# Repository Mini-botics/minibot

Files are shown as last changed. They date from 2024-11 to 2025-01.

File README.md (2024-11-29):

# Minibot
An open-source, ROS-compatible mini robot project designed for educational purposes. Ideal for learning robotics, experimenting with ROS, or personal projects. 



## Unique Features
- **Robust and Customizable**: Offers modularity for customization with readily available components that are easy to replace or upgrade. Supports various locomotion types, including differential, 4 wheel and holonomic drive systems, allowing for customizable movement options.



- **Minimal Cable Design**: All key components (battery, charger, BMS, etc.) are integrated into a single robot using a custom PCB, minimizing wiring while ensuring both efficiency and durability.





- **Easy-to-Use**: Designed to be user-friendly for beginners while still offering enough complexity for advanced users to explore.

- **Affordable**: Engineered to be a cost-effective option for students and hobbyists alike, without sacrificing quality or performance.

## Getting Started
To get started with the robot, please follow this video documentation.

IMAGE ALT TEXT HERE (https://www.youtube.com/watch?v=GUFT_sU2eYY&t)

You can also check our [youtube channel](https://www.youtube.com/@minibotics). 

Please note that this is an open-source project, and we welcome contributions and suggestions from the community.

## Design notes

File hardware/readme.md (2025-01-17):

# Bill of Materials (BOM)

This project requires several components to build. The detailed Bill of Materials (BOM), including quantities, descriptions, and purchase links, is hosted on Google Sheets for easy access and updates.

[View the Bill of Materials on Google Sheets](https://docs.google.com/spreadsheets/d/1GKpQS9YWHXVLVaMREtha1JvgfUiriMxIkeRr4HUK7rA/edit?usp=sharing)

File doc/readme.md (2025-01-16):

# minibot PCB Design Files

Access the design files for various layers and components of the minibot project using the links below:

- **[Base Layer Design Files](https://oshwlab.com/rstmsvk/mini_copy_copy_copy_copy_copy_copy_copy_copy_copy_copy_copy)**  
  The base layer design files of the minibot.

- **[Proto Layer Design Files](https://oshwlab.com/rstmsvk/mini_copy_copy_copy_copy_copy_copy_copy_copy_copy_copy_copy_copy)**  
  The proto layer design files for the minibot.

- **[Encoder Design Files](https://oshwlab.com/rstmsvk/mini_copy_copy_copy_copy_copy_copy_copy_copy_copy_copy_copy_copy_copy_copy)**  
  The encoder design files for the minibot.

- **[Proto Board Design Files](https://oshwlab.com/rstmsvk/mini_copy_copy_copy_copy_copy_copy_copy_copy_copy_copy_copy_copy_copy)**  
  Design files for the proto board used in the minibot project.

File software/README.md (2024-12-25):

# Minibot Software
The software section of the Minibot is organized into specific folders, each serving a unique purpose, as detailed below:

**romer-minibot**: 
   - This folder contains the Pico library with wireless communication capabilities. 
   - Use this if your project requires network communication for the robot.

**romer-minibot-lite**: 
   - This folder contains a simpler version of the Pico library without wireless communication capabilities.
   - Use this version for offline or standalone functionality.

**MiniROS**:
   - This folder contains the ROS (Robot Operating System) part of the project.
   - Check this folder if you are integrating ROS into your robot project.

## Getting Started

- To integrate wireless communication, navigate to the `romer-minibot` folder and follow the setup instructions provided there.
- For a lightweight, offline version, explore the `romer-minibot-lite` folder.
- To explore the ROS implementation, check the `MiniROS` folder.

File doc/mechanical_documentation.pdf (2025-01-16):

# ME462 MECHATRONIC DESIGN

# Mini Robot Documentation

# Version 1.0

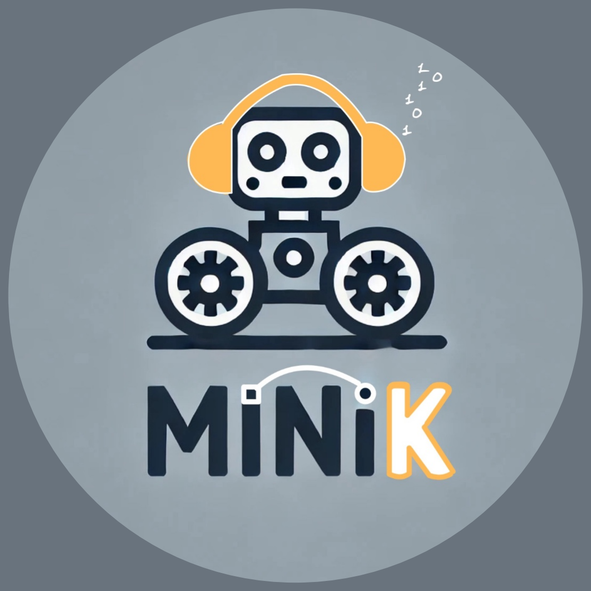
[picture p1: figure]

### MECHANICAL DOCUMENTATION

## Table of Contents

1 Introduction | 2
2 Component List | 2
3 Print Instructions | 2
3.1 Battery Holders | | 2
3.2 Wheels | | 3
3.3 Motor Holders | | 4
3.4 Camera Holder | | 4

## List of Figures

1 | First Pause Layer | | 2
2 | Second Pause Layer | | 3
3 | Wheel Pause Layer | | 3
4 | Print orientation | | 4
5 | Pause Layer | | 4

## 1 Introduction

This document provides a comprehensive guide for the assembly and implementation of the minibot designed for educational purposes.

## 2 Component List

The following components are included in the mechanical design:

- Battery Holders
- Motor Holders
- Wheel (with or without magnets)
- Caster Wheel
- Camera Holder

## 3 Print Instructions

### 3.1 Battery Holders

- Two printouts of this part need to be taken: the part itself and the mirror symmetry.
- This part has internal M3 nuts for mounting.
- The printing process must be paused, then these nuts must be added to part. After that printing process can be resumed. In this way, the embedded nuts can be reached.

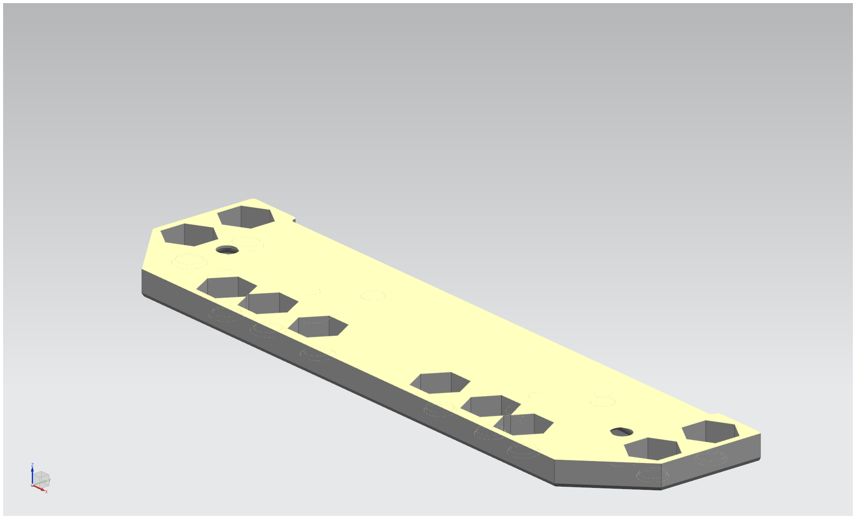
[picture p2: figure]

Figure 1: First Pause Layer

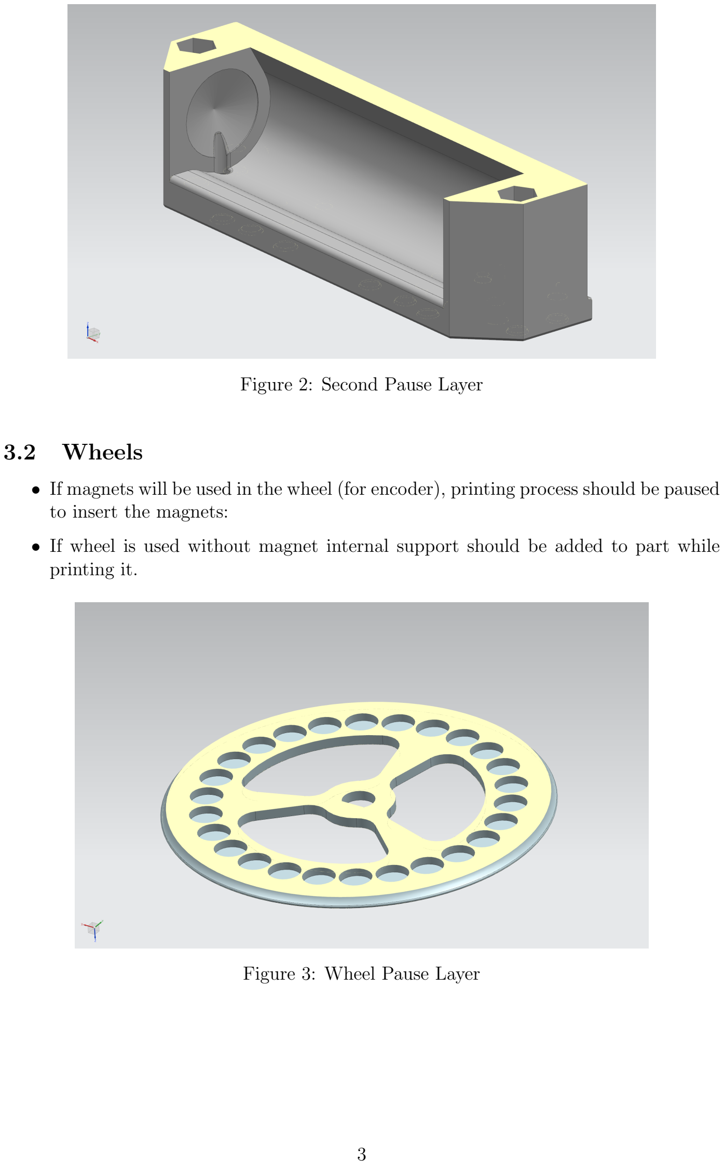
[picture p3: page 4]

Figure 2: Second Pause Layer

### 3.2 Wheels

- If magnets will be used in the wheel (for encoder), printing process should be paused to insert the magnets:
- If wheel is used without magnet internal support should be added to part while printing it.

Figure 3: Wheel Pause Layer

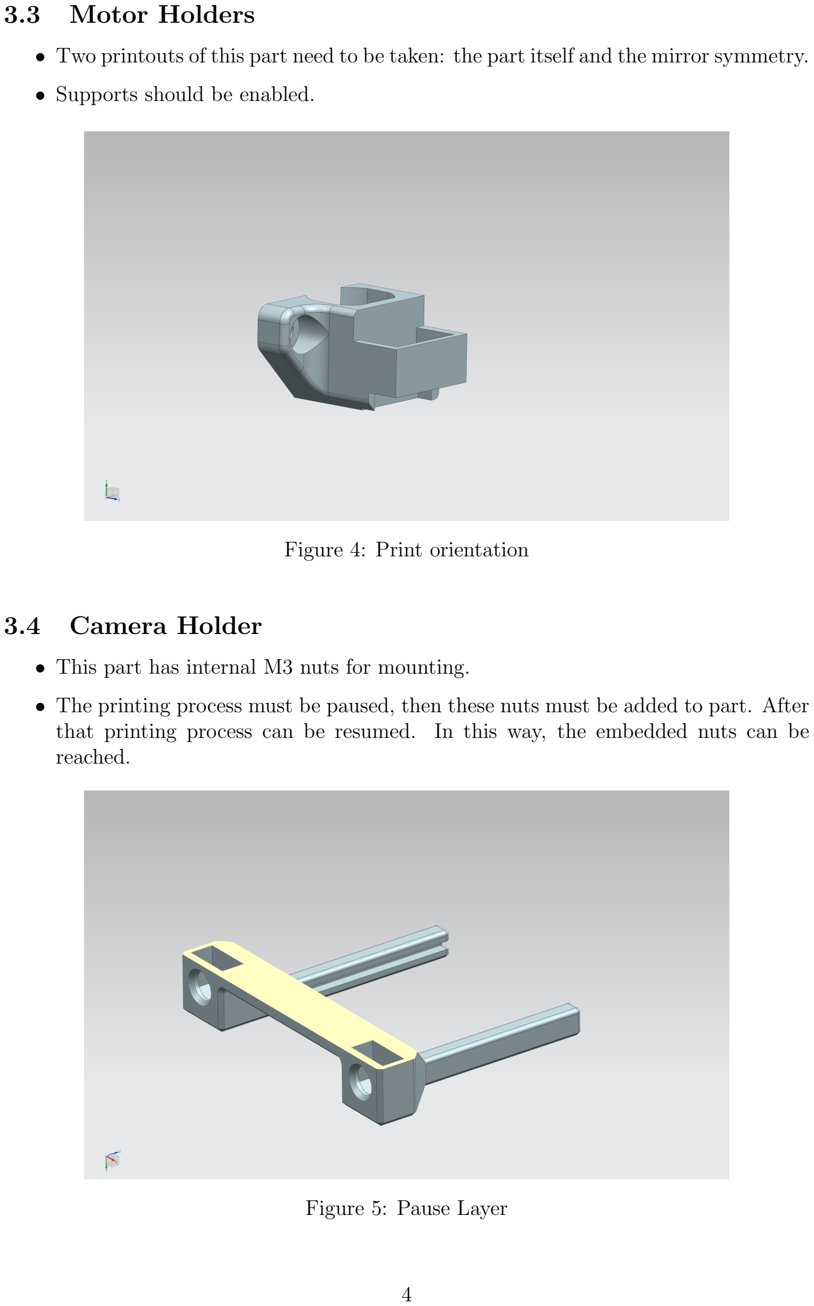
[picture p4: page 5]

### 3.3 Motor Holders

- Two printouts of this part need to be taken: the part itself and the mirror symmetry.
- Supports should be enabled.

Figure 4: Print orientation

### 3.4 Camera Holder

- This part has internal M3 nuts for mounting.
- The printing process must be paused, then these nuts must be added to part. After that printing process can be resumed. In this way, the embedded nuts can be reached.

Figure 5: Pause Layer

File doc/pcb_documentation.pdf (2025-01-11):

# ME462 MECHATRONIC DESIGN

# Mini Robot Documentation

# Version 1.0


### PCB DOCUMENTATION

## Table of Contents

1 Introduction | 2
2 PCB Overview | 2
3 Component List | 2
4 Connectors and Pin Configuration | 2
5 Motor Configurations | 3
6 Power Supply | 4
7 Mounting Instructions | 4
8 Usage and Applications | 4
9 Maintenance and Troubleshooting | 5

## 1 Introduction

This document provides a comprehensive guide for the usage and implementation of the mini base PCB designed for educational purposes. It includes details on the components, connectors, motor configurations, and power supply requirements.

## 2 PCB Overview

The mini base PCB is designed to be a compact and versatile platform for developing desk robots. It supports through-hole components and pre-made modules to ensure ease of use and accessibility for both students and researchers.

The design files can be accessed using the corresponding links:

- miniRobot Base Layer: Base Layer Design Files (https://oshwlab.com/rstmsvk/mini_copy_copy_copy_copy_copy_copy_copy_copy_copy_copy_copy)
- miniRobot Proto Layer: Proto Layer Design Files (https://oshwlab.com/rstmsvk/mini_copy_copy_copy_copy_copy_copy_copy_copy_copy_copy_copy_copy)
- miniRobot Encoder: Encoder Design Files (https://oshwlab.com/rstmsvk/mini_copy_copy_copy_copy_copy_copy_copy_copy_copy_copy_copy_copy_copy_copy)
- Proto Board: Proto Board Design Files (https://oshwlab.com/rstmsvk/mini_copy_copy_copy_copy_copy_copy_copy_copy_copy_copy_copy_copy_copy)

## 3 Component List

The following components are included in the PCB design:

- Raspberry Pi Pico W
- N20 DC Motors (Up to 4)
- XH 2.54 connectors for power and data
- XL4005 voltage regulator
- TP5100 charger module
- ADXL345 accelerometer
- HC-SR04 ultrasonic sensor
- 18650 Li-Ion battery
- Hall sensors

## 4 Connectors and Pin Configuration

The PCB has multiple connectors and pins for various components. Below are the details for each connector and its corresponding pins:

### 4.1 Connectors

- H1, H2, H3, H4, H5, H6, H7, H8: Connectors for hall sensor encoders.
- B1, B2: Bumper connectors.

- SW1: Reset switch.
- M1, M2, M3, M4, M5, M6, M7, M8, M9, M10. Motor locations for different configurations

### 4.2 Pin Configuration

Corresponding pin numbers can be found in the schematic of the base PCB.

- PICO W GPIO Pins:

– GPIO 0 to GPIO 28: General purpose input/output pins.

– VSYS: Power supply pins.

– GND: Ground pins.

- Motor Connectors (MI1 to MI8):

– MI1: Motor input 1

– MI2: Motor input 2

– MI3: Motor input 3

– MI4: Motor input 4

– MI5: Motor input 5

– MI6: Motor input 6

– MI7: Motor input 7

– MI8: Motor input 8

- Motor Outputs (MO1 to MO8):

– MO1: Motor output 1

– MO2: Motor output 2

– MO3: Motor output 3

– MO4: Motor output 4

– MO5: Motor output 5

– MO6: Motor output 6

– MO7: Motor output 7

– MO8: Motor output 8

## 5 Motor Configurations

Depending on the configuration and the number of motors used, the following pins should be connected:

### 5.1 Dual Motor Configuration

- Rear Traction Motor M7 and M9 should be used.
- Center Traction Motor M1 and M2 should be used.

### 5.2 Triple wheel configuration

. Either motors M1 and M7, M10 or M2 and M8, M9 should be used.

### 5.3 Quadruple wheel configuration

Motors M8, M9 and M7, M10 should be used.

## 6 Power Supply

IMPORTANT! THE VOLTAGE REGULATOR SHOULD BE SET TO 5V BEFORE CONNECTING IT TO THE PCB OR SET IT BY INCREMENT-ING THE VOLTAGE.

The PCB operating voltage is a 5V. The XL4005 voltage regulator ensures stable output for the components. Additional filtering capacitors can be added. The TP5100 module is used for charging the connected batteries. Thus feed voltage for the PCB should be between 9V and 15V.

## 7 Mounting Instructions

To ensure proper assembly and functionality of the PCB, follow the steps below for mounting the components:

1. First, mount the BMS (Battery Management System).
2. Next, mount the TP5100 charger module.
3. Then, mount the HC-SR04 ultrasonic sensor.
4. Then, mount dip switch.
5. If front encoder connectors will be used they should be mounted at this step.
6. After that, mount the XL4005 voltage regulator.
7. Since order is not important for the rest of the components mount them based on your specific requirements and preferences.

## 8 Usage and Applications

This PCB can be used for various educational and research purposes, including but not limited to:

- Desk robots for student experiments.

- Robotics research in higher education.
- Prototype development for motor control systems.

## 9 Maintenance and Troubleshooting

Regular maintenance includes checking connections and ensuring that all components are securely attached. Troubleshooting steps for common issues are as follows:

- No Power: Check the power supply connections and the voltage regulator.
- Motor Not Working: Verify motor connections and check the corresponding driver outputs.
- Sensor Issues: Ensure proper connection to the GPIO pins and verify sensor functionality.

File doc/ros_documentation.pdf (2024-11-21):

# ME462 MECHATRONIC DESIGN

# Mini Robot Documentation

# Version 1.0


We understand that reading documentation can be challenging, especially when you’re eager to dive into the hands-on work. However, taking the time to read the documentation can save you a lot of time in the long run and prevent costly mistakes. That’s why we strongly recommend following the documentation carefully..

i

## MINI ROBOT PROJECT ROS Entegration

## Table of Contents

1 Introduction | 1
2 Getting Started | 1
3 Project structure | 2
4 Answer Key | 8

## List of Figures

## List of Tables

ii

## 1 Introduction

The ROS part of this documentation is not intended to provide an in-depth tutorial on ROS. Its primary objective is to kickstart your ROS learning journey by guiding you through the basic examples using our mini robot, allowing you to see the ROS structure in action and enabling you to apply what you learn directly with our robot.

In the following sections, you will find the installation steps, an overview of the project structure, basic examples, and a more advanced example. Even if you are already familiar with ROS, I highly recommend reviewing the project structure to understand how it is organized, which will help you add your own improvements effectively.

## 2 Getting Started

### 2.1 Installation

To be able to get start the ROS part of project, followings must be installed.

Note

Be sure that you have a compatible version of Ubuntu for ROS2 Humble. If not, it should downloaded to Docker. This document doesn’t include Docker installation instructions, but it can be found easily on the internet.

ROS2 Humble

Official installation can be followed: https://docs.ros.org/en/humble/Installation/Ubuntu-Install-Debians.html (https://docs.ros.org/en/humble/Installation/Ubuntu-Install-Debians.html)

Ad ”opt/ros/humble/setup.bash” to the bashrc to source the enviroment for ROS when the restart, otherwise one must source in every case:

sudo nano ~/. bashrc

Listing 1: Source setup

Clone the Mini Robot ROS Repository

Clone the repository containing the mini robot’s ROS packages:

git clone https :// github . com / ZNeslisah / MiniROS . git

Listing 2: Cloning the Mini Robot Repository

Setup for Workspace

After downloading workspace you need to

cd MiniROS / dew_ws
colcon build -- symlink - install source install / setup . bash

Listing 3: Setting up Workspace

Note

- colcon build is used to build packages in a ROS 2 workspace. It compiles the source code, generates necessary build files, and prepares the packages for use. YOU SHOULD RUN EVERY TIME WHEN YOU MAKE CHANGE (With adding ”–symlink-install” no need to do when there is adjustment on pre existing file, run when there is new file.)
- source is used to set up the environment for a ROS 2 workspace. Running source install/setup.bash configures the shell to recognize the built packages, enabling you to run nodes and use the tools provided by the packages. YOU SHOULD RUN EVERY TIME YOU OPEN A NEW TERMINAL
- If you have other friends who are also using ROS, and connected to same internet. You can choose to add export ROS DOMAIN ID=*number from 1 to 100* to your the bashrc. This will seperate your communication and prevent you from mistakenly get messages from other peoples.

Additional Setup

Some simulation enviroments and packages must be installed to run the project. I won’t directly list them. You can follow the errors and install these when required.

If you have done all the installation until that point, lets run our first launch file:

ros2 launch mini_robot letsStart . launch . py

Listing 4: Running the Launch File

Recommendation

I highly recommend exploring tmux for managing multiple terminal sessions within a single window. Although its keyboard shortcuts may seem challenging at first, mastering them will greatly simplify handling multiple terminals, which is often necessary when working with ROS.

## 3 Project structure

The project is divided into four main sections, as shown in the figure below:

- mini robot: This section contains configurations and description of the mini robot and the core functionalities.
- mini control: This section includes the control logic for the mini robot. It manages the robot’s movements and responses based on sensor inputs and tracking data.

- aruco tracker: This section is responsible for detecting and tracking ArUco markers. It includes nodes and configurations for processing camera input and identifying marker positions.
- ball tracker: This section handles the detection and tracking of a ball. It includes the necessary algorithms and nodes to track the ball’s movement using image processing techniques.

The following sections will show the project structure and give small examples. We will start with using mini robot package, but if you are familiar with ROS and want to directly start using it with hardware, you can skip the mini control section.

### 3.1 mini robot

### 3.1.1 Simulation Environments

Before diving into the examples, the following programs should be introduced:

- Gazebo: It is a powerful robotics simulator that provides an accurate environment to test robots in both indoor and outdoor settings. It offers physics-based simulation with real-world effects such as gravity, friction, and sensor noise.

One can simply write ”gazebo” to terminal to open a empty gazebo file, but it can be done more with following command

ros2 launch mini_robot launch_sim . launch . py

Listing 5: Meeting with Gazebo enviroment

- Rviz: It is a 3D visualization tool used in ROS for visualizing sensor data, robot models, and other aspects of the robot’s environment. It provides an interactive interface to visualize what the robot perceives, such as laser scans, camera feeds, and point clouds, and allows users to monitor the robot’s state and debug issues effectively. RViz is primarily used for real-time monitoring and analysis of robot operations.

Now, open the Rviz and see our robot in there:

rviz2 -d src / mini_robot / config / main . rviz

Listing 6: Meeting with Rviz enviroment

Note

In the above code we have called the rviz2 with pre-build configuration. One can also open rviz2 with only writting rviz2, but in that case the robot model, camera and TF should be added manually with add button in left corner. You should also adjust the fixed frame and the topic names for all added parts.

The mini robot package includes numerous configuration and description files that define the robot for simulation purposes. While these files won’t be explained in this documentation, you have the option to explore their types and structures to gain further insights into how the robot is configured and simulated.

Recommendation

In mini robot package, I have utilized from the tutorial of Articulated Robotics. It was clear and comprehensive tutorial, you can check it if you want. But be careful that this tutorial uses ros2 control while we are using custom communication protocol. Checking our protocol is optional and not necessary for understanding ROS implementation or learning, but ensure that the protocol is correctly downloaded onto your Pico device. Check the COMMMMMMM part for that. https://youtube.com/playlist?list=PLunhqkrRNRhYAffV8JDiFOatQXuU-NnxT&si=yRpMbUpwmb8o5 (https://youtube.com/playlist?list=PLunhqkrRNRhYAffV8JDiFOatQXuU-NnxT&si=yRpMbUpwmb8o5)

### 3.1.2 teleop twist keyboard

Let’s try to drive our robot using builtin package of Ros. Run the following command, read the instruction afterwards since the control is a bit weird. If you have closed the gazebo and rviz, you should reopen them for visualization.

ros2 run teleop_twist_keyboard teleop_twist_keyboard -- ros - args -- remap / cmd_vel :=/ cmd_vel_teleop

Listing 7: Meeting with Rviz enviroment

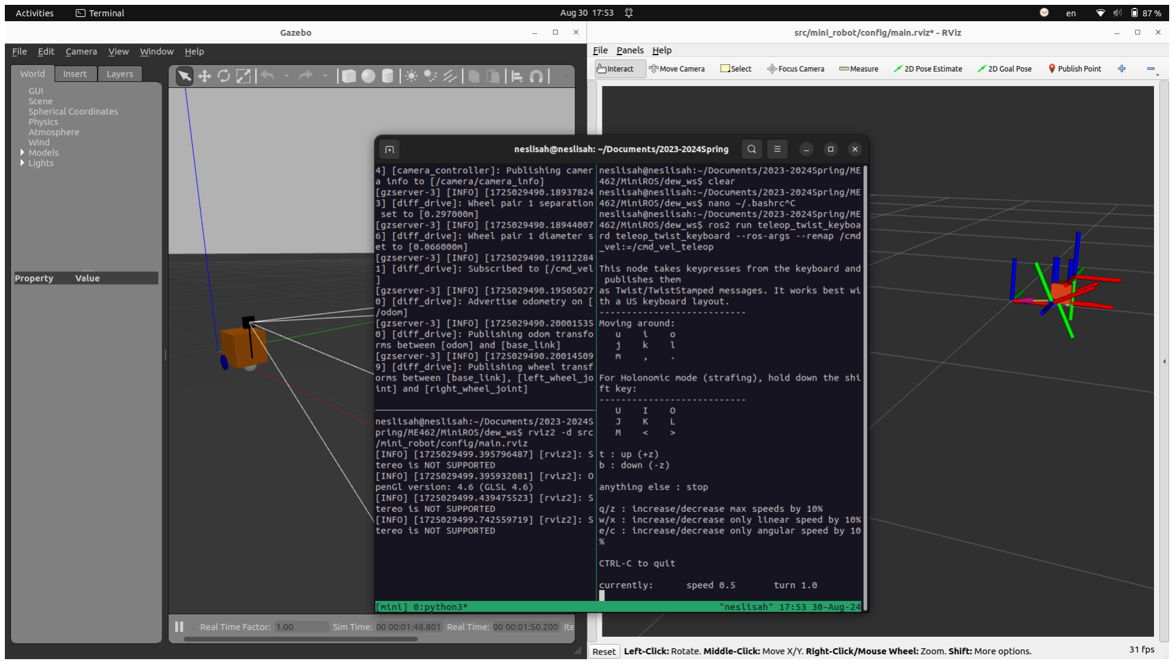
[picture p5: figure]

### 3.1.3 Launch files

You have done first interraction with a mini robot, before skipping to other package, the launch files should be mentioned:

- letsStart.launch.py

You have already run this launch file, it’s only purpose is printing loginfo to the screen.

- launch sim.launch.py

You have also already run this launch file and observe the robot in similation. It is the launch file which is openning Gazebo enviroment.

- launch robot.launch.py

We haven’t talked about this launch file so far. It’s only difference from launch sim.launch.py is that it is not opening similation enviroment.

- rsp.launch.py

It is the launch file which is openning builtin ROS robot state publisher package.

Note

The robot state publisher is a ROS package that publishes the state of a robot to the rest of the ROS ecosystem. It uses the robot’s URDF (Unified Robot Description Format) model to compute and broadcast the positions of all the robot’s joints and links in real-time.

- joystick.launch.py

We won’t use joystick, but launch setup is provided. If one wants to add that functionality to robot, he or she can use the setup.

- ball tracker.launch.py

It is the launch file for ball tracker mode of the robot.

Exercise

### 3.1 Before going to start with actual robot, can you run the ball tracker node? Don’t

forget that you should also open simulations. In the repo there is pre built enviroment with balls for gazebo. You should run the gazebo with that configuration. When running ball tracker add ”sim mode:=true” after ”ball tracker.launch.py” keyword.
Answer key is at the end of the documentation

### 3.2 mini control

This is the package which we will start to use our mini robot. Before proceed make sure that you have downloaded our communication package in to your pico wireless.

### 3.2.1 Nodes

First two nodes are responsible from the communication with pico.

- pipe read

Messages are get from the pico and converted to Ros topics.

- pipe write

Ros topics are converted to communication protocol messages and send it to pico.

- emergency button

Emergency callback, when the button is pushed it stops the car and and activate emergency leds.

- bumper

When mini robot hits its bumper, it stops the car and activate the bumper leds.

- battery

Responsible from showing the battery level with publishing brightness value. In neopixel node brightness value is turned into color between green and red.

- neopixel

Listen all the boolean led messages and send the pixel colors to the pipe write.

Note

When adding additional nodes to the project, you can utilize the same topics used in pixel write and pipe read, ensuring seamless integration without modifying the existing communication flow. However, if modifications are required for pipe write or pipe read, it is essential to adjust the communication protocol on the Pico accordingly to maintain compatibility and ensure correct data transmission.
Do not forget to add new created files in to setup.py file.

Exercise

### 3.2 After reviewing the nodes, you can proceed to run the emergency node. Check

to see if it correctly stops when the button is pressed. Run the nodes with ros2 run package name node name

Have you noticed that even running basic functionalities in ROS requires multiple terminals? This highlights the importance of launch files. Launch files allow us to start multiple nodes simultaneously, streamlining the process and enhancing efficiency.

For example, try to run ros2 launch mini control emergency launch.py instead of last 4 lines of answer key.

How to use joystick for control?

Install the evtest to check the connection. After running evtest, try to push the joystick buttons, you should see the reactions if your connection is successful.

sudo apt install joystick jstest - gtk evtest
evtest

Listing 8: Install evtest

Check to joy node to ensure that everything work perfectly. Run the followings in 2 seperate lines. When press the button you should see that topic output is changed.

ros2 run joy joy_enumerate_devices
ros2 topic echo / joy

Listing 9: Check joystick with ROS

Recommendation

If you want to see the which buttons corresponding to which numbers. You can use Josh Newans joy tester node. $https://github.com/joshnewans/joy_tester. git$

Exercise

### 3.3 Can you control the actual robot with joystick now? Search for the needed

launch files and nodes, choose proper ones.

## 4 Answer Key

The lines on answer keys should run on seperate terminals.

3.1

ros2 launch mini_robot launch_sim . launch . py world :=./ src / mini_robot / worlds / obstacles . world
rviz2 -d src / mini_robot / config / main . rviz
ros2 launch mini_robot ball_tracker . launch . py sim_mode := true

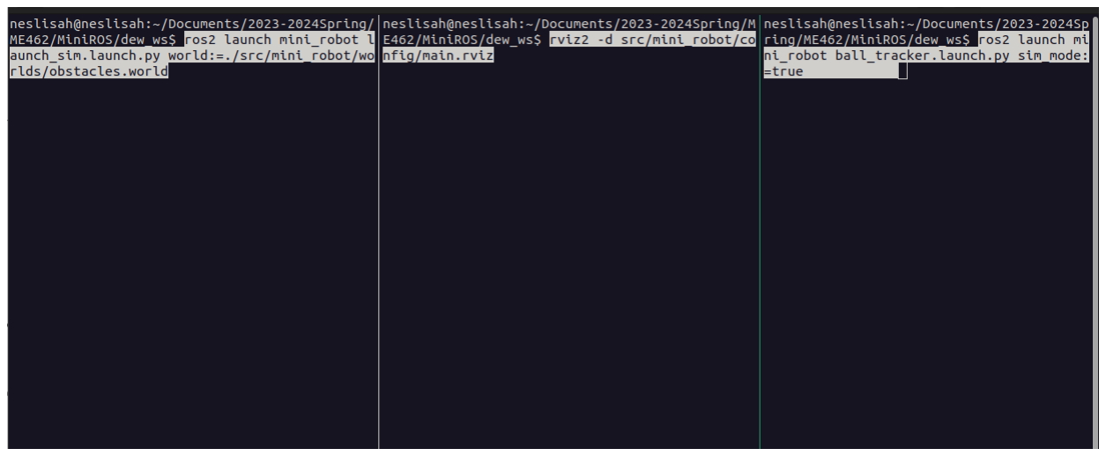
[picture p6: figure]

3.2

ros2 launch mini_robot launch_sim . launch . py world :=./ src / mini_robot / worlds / obstacles . world
ros2 run teleop_twist_keyboard teleop_twist_keyboard -- ros - args -- remap / cmd_vel :=/ cmd_vel_teleop
ros2 run mini_control pipe_write
ros2 run mini_control pipe_read
ros2 run mini_control emergency_button ros2 run mini_control neopixel

3.3

ros2 launch mini_robot launch_robot . launch . py ros2 launch mini_robot joystick . launch . py ros2 run mini_control pipe_write

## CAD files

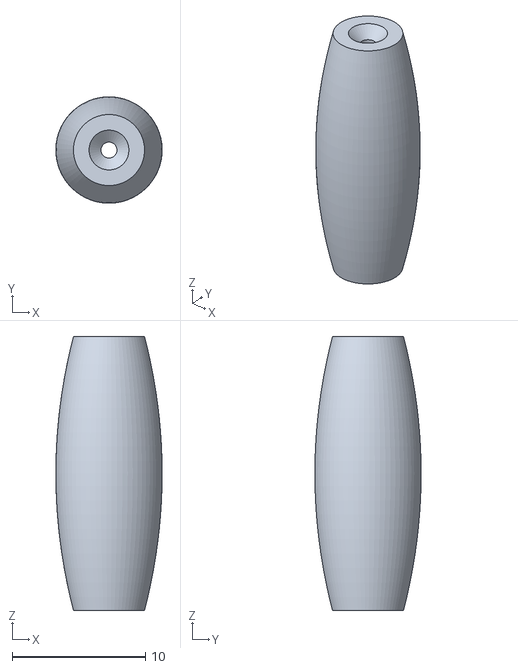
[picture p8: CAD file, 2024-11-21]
hardware/cad/wheels/holonomic/Roller.STL
8.00 x 7.99 x 20.6

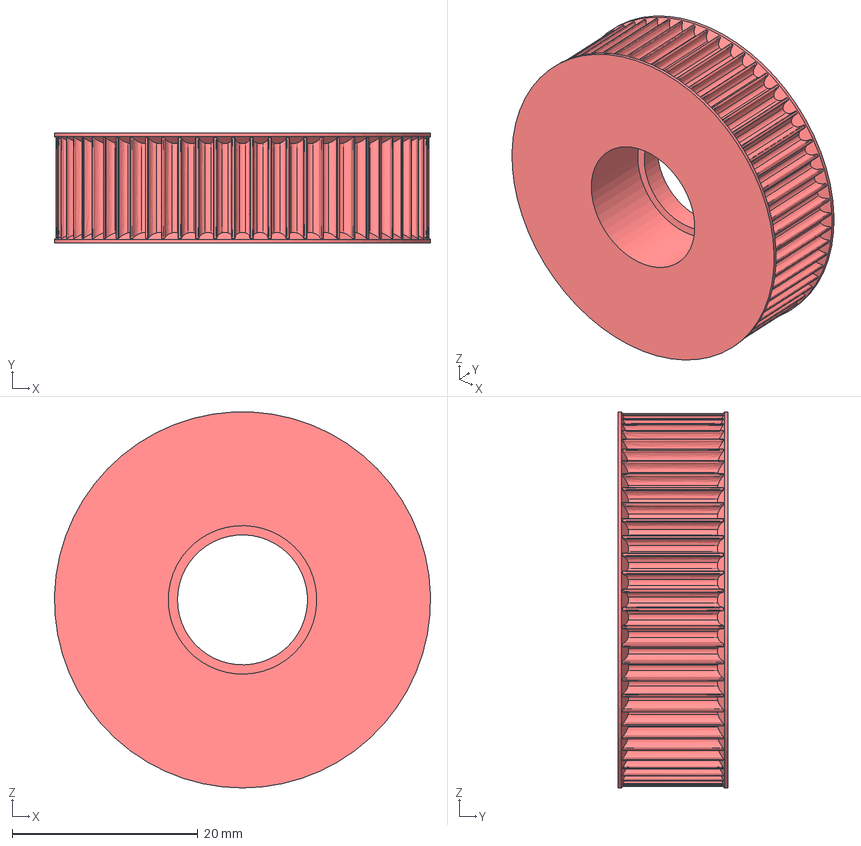
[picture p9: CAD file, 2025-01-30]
hardware/cad/wheels/traction_wheel.step
40.5 x 11.9 x 40.5 mm

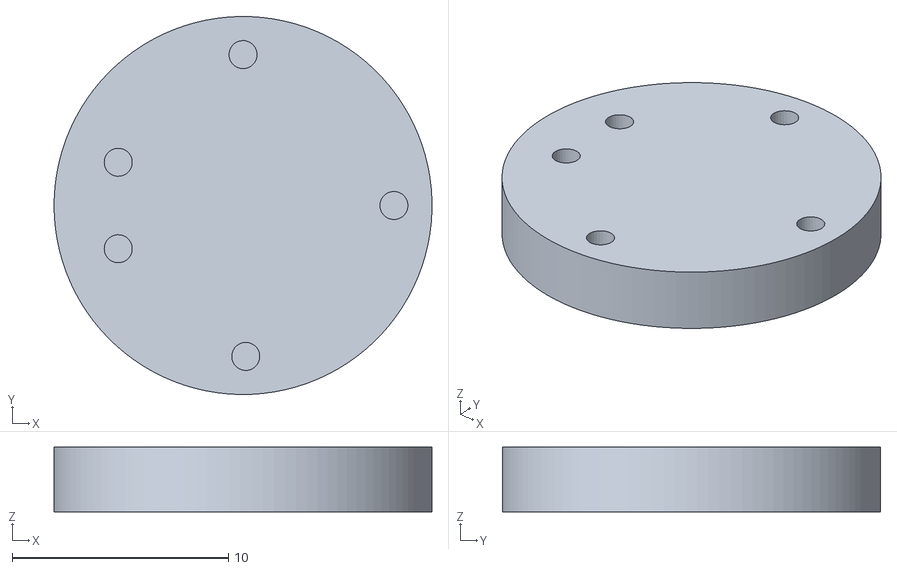
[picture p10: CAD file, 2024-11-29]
hardware/tools/bms_solder_jig.stl
17.5 x 17.5 x 3.00

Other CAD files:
hardware/cad/wheels/idler_wheel.step
hardware/cad/battery_holder/battery_holder.prt
hardware/cad/motor_holders/idler_holder.prt
hardware/cad/motor_holders/motorholder_corner_with_encoder.prt
hardware/cad/motor_holders/motorholder_corner_without_encoder.prt
hardware/cad/motor_holders/motorholder_cross_corner_without_encoder.prt
hardware/cad/motor_holders/motorholder_middle_without_encoder.prt
hardware/cad/rpi_accesories/camholder.prt
hardware/cad/rpi_accesories/pi_spacer.prt
hardware/cad/rpi_accesories/pi_spacer_snap_in.prt
hardware/cad/wheels/midcaster_point_contact.prt
hardware/cad/wheels/midcaster_roller.prt
hardware/cad/wheels/midcaster_with_bearing.prt
hardware/cad/wheels/wheel_with_magnets.prt

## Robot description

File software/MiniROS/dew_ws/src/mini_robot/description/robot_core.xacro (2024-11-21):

<?xml version="1.0"?>
<robot xmlns:xacro="http://www.ros.org/wiki/xacro" >

    <xacro:include filename="inertial_macros.xacro"/>


    <xacro:property name="chassis_length" value="0.09"/> 
    <xacro:property name="chassis_width" value="0.09"/> 
    <xacro:property name="chassis_height" value="0.09"/> 
    <xacro:property name="chassis_mass" value="0.5"/>  
    <xacro:property name="wheel_radius" value="0.0215"/>  
    <xacro:property name="wheel_thickness" value="0.004"/> 
    <xacro:property name="wheel_mass" value="0.05"/>
    <xacro:property name="wheel_offset_x" value="0.01024"/> 
    <xacro:property name="wheel_offset_y" value="0.047"/> 
    <xacro:property name="wheel_offset_z" value="0.0"/>
    <xacro:property name="caster_wheel_radius" value="0.018"/> 
    <xacro:property name="caster_wheel_mass" value="0.001"/>
    <xacro:property name="caster_wheel_offset_x" value="0.07"/> 
    <xacro:property name="caster_wheel_offset_z" value="${wheel_offset_z - wheel_radius + caster_wheel_radius}"/>  
    

    
    <material name="white">
        <color rgba="1 1 1 1" />
    </material>

    <material name="orange">
        <color rgba="1 0.3 0.1 1"/>
    </material>

    <material name="blue">
        <color rgba="0.2 0.2 1 1"/>
    </material>

    <material name="black">
        <color rgba="0 0 0 1"/>
    </material>

    <material name="red">
        <color rgba="1 0 0 1"/>
    </material>

    <!-- BASE LINK -->

    <link name="base_link">

    </link>

    <!-- BASE_FOOTPRINT LINK -->

    <joint name="base_footprint_joint" type="fixed">
        <parent link="base_link"/>
        <child link="base_footprint"/>
        <origin xyz="0 0 0" rpy="0 0 0"/>
    </joint>

    <link name="base_footprint">
    </link>


    <!-- CHASSIS LINK -->

    <joint name="chassis_joint" type="fixed">
        <parent link="base_link"/>
        <child link="chassis"/>
        <origin xyz="${-wheel_offset_x} 0 ${-wheel_offset_z}"/>
    </joint>

    <link name="chassis">
        <visual>
            <origin xyz="${chassis_length/2} 0 ${chassis_height/2}"/>
            <geometry>
                <box size="${chassis_length} ${chassis_width} ${chassis_height}"/>
            </geometry>
            <material name="orange"/>
        </visual>
        <collision>
            <origin xyz="${chassis_length/2} 0 ${chassis_height/2}"/>
            <geometry>
                <box size="${chassis_length} ${chassis_width} ${chassis_height}"/>
            </geometry>
        </collision>
        <xacro:inertial_box mass="0.5" x="${chassis_length}" y="${chassis_width}" z="${chassis_height}">
            <origin xyz="${chassis_length/2} 0 ${chassis_height/2}" rpy="0 0 0"/>
        </xacro:inertial_box>
    </link>

    <gazebo reference="chassis">
        <material>Gazebo/Orange</material>
    </gazebo>

    <!-- LEFT WHEEL LINK -->

    <joint name="left_wheel_joint" type="continuous">
        <parent link="base_link"/>
        <child link="left_wheel"/>
        <origin xyz="0 ${wheel_offset_y} 0" rpy="-${pi/2} 0 0" />
        <axis xyz="0 0 1"/>
    </joint>

    <link name="left_wheel">
        <visual>
            <geometry>
                <cylinder radius="${wheel_radius}" length="${wheel_thickness}"/>
            </geometry>
            <material name="blue"/>
        </visual>
        <collision>
            <geometry>
                <sphere radius="${wheel_radius}"/>
            </geometry>
        </collision>
        <xacro:inertial_cylinder mass="${wheel_mass}" length="${wheel_thickness}" radius="${wheel_radius}">
            <origin xyz="0 0 0" rpy="0 0 0"/>
        </xacro:inertial_cylinder>
    </link>

    <gazebo reference="left_wheel">
        <material>Gazebo/Blue</material>
    </gazebo>




    <!-- RIGHT WHEEL LINK -->

    <joint name="right_wheel_joint" type="continuous">
        <parent link="base_link"/>
        <child link="right_wheel"/>
        <origin xyz="0 ${-wheel_offset_y} 0" rpy="${pi/2} 0 0" />
        <axis xyz="0 0 -1"/>
    </joint>

    <link name="right_wheel">
        <visual>
            <geometry>
                <cylinder radius="${wheel_radius}" length="${wheel_thickness}"/>
            </geometry>
            <material name="blue"/>
        </visual>
        <collision>
            <geometry>
                <sphere radius="${wheel_radius}"/>
            </geometry>
        </collision>
        <xacro:inertial_cylinder mass="${wheel_mass}" length="${wheel_thickness}" radius="${wheel_radius}">
            <origin xyz="0 0 0" rpy="0 0 0"/>
        </xacro:inertial_cylinder>
    </link>

    <gazebo reference="right_wheel">
        <material>Gazebo/Blue</material>
    </gazebo>


    <!-- CASTER WHEEL LINK -->

    <joint name="caster_wheel_joint" type="fixed">
        <parent link="chassis"/>
        <child link="caster_wheel"/>
        <origin xyz="${caster_wheel_offset_x} 0 ${caster_wheel_offset_z}"/>
    </joint>


    <link name="caster_wheel">
        <visual>
            <geometry>
                <sphere radius="${caster_wheel_radius}"/>
            </geometry>
            <material name="white"/>
        </visual>
        <collision>
            <geometry>
                <sphere radius="${caster_wheel_radius}"/>
            </geometry>
        </collision>
        <xacro:inertial_sphere mass="${caster_wheel_mass}" radius="${caster_wheel_radius}">
            <origin xyz="0 0 0" rpy="0 0 0"/>
        </xacro:inertial_sphere>
    </link>

    <gazebo reference="caster_wheel">
        <material>Gazebo/White</material>
        <mu1 value="0.001"/>
        <mu2 value="0.001"/>
    </gazebo>

</robot>

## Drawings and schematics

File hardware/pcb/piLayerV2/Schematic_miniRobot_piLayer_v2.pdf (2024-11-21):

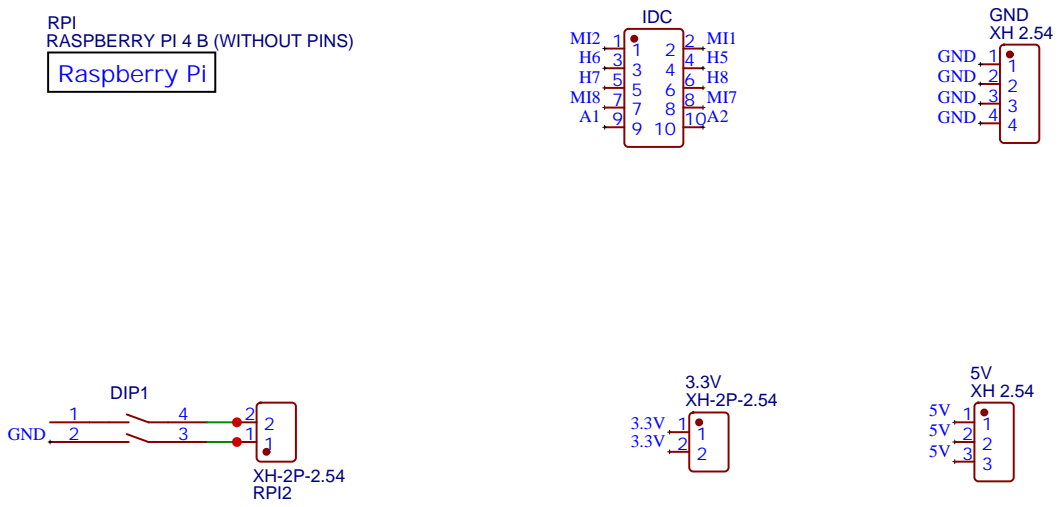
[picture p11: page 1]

RPI
RASPBERRY PI 4 B (WITHOUT PINS)
Raspberry Pi

Drawn By: rustem sevik

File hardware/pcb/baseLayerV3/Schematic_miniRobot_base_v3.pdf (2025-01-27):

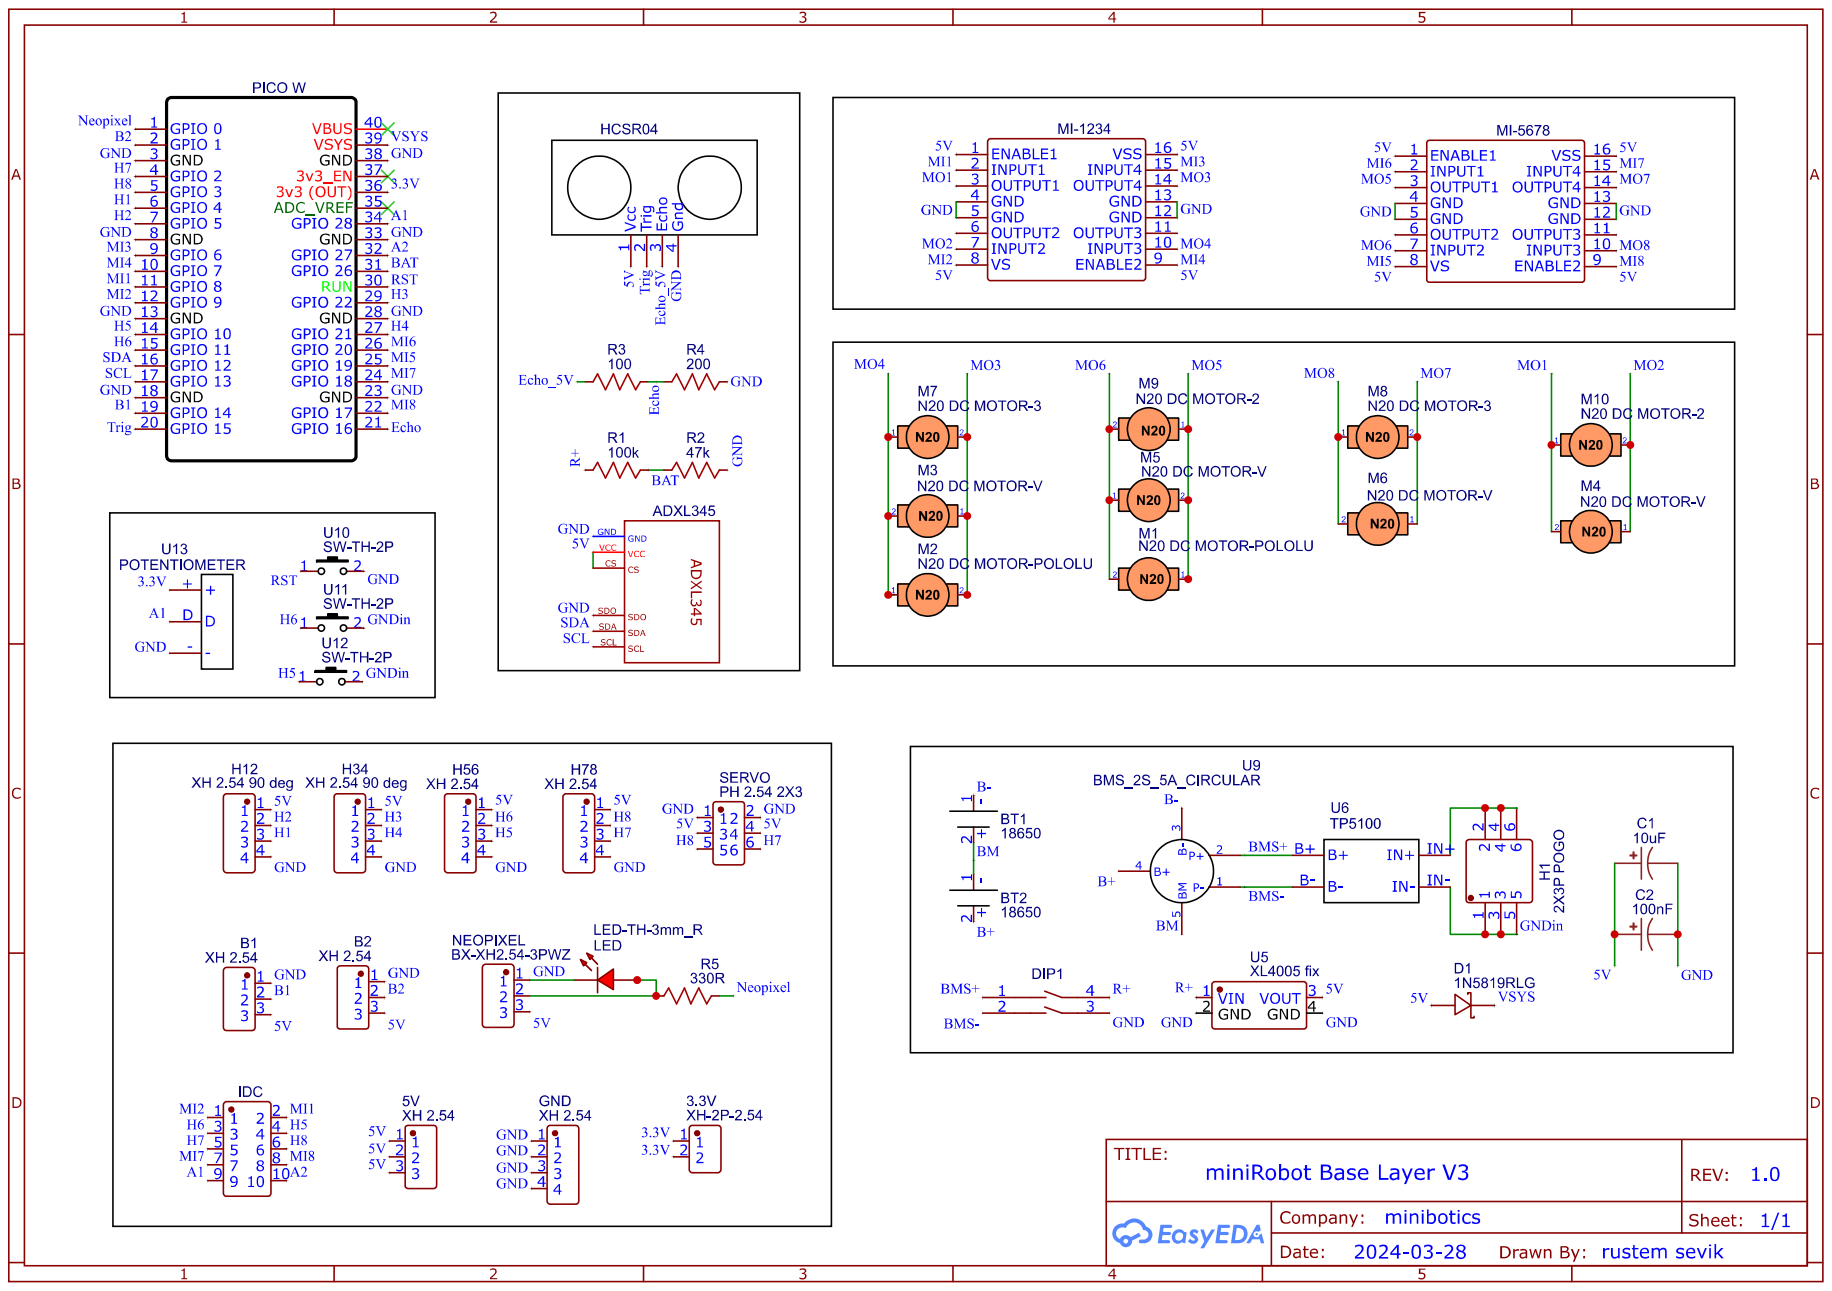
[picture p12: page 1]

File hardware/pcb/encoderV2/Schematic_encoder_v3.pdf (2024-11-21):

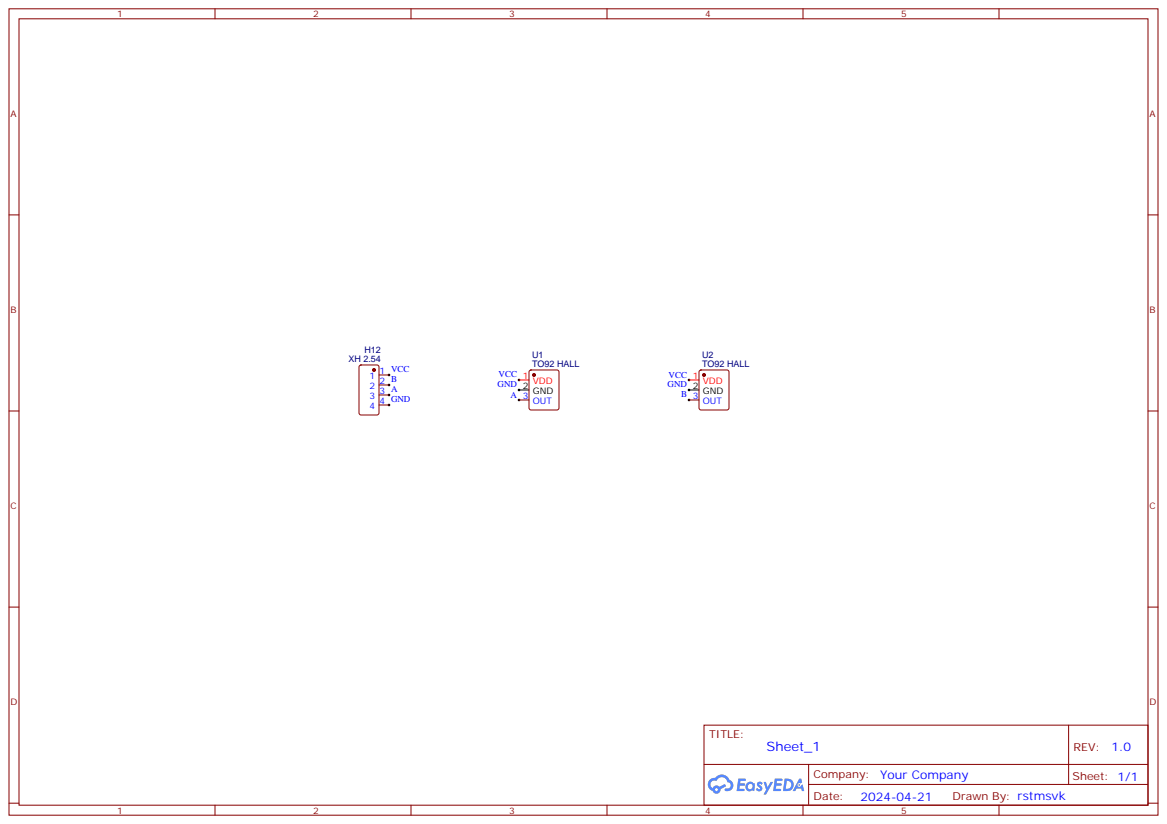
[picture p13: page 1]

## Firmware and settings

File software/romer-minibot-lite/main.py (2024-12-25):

from machine import Pin, I2C
import time
from romer_minibot_lite import Accelerometer  # Assuming Accelerometer is saved as accelerometer.py
from romer_minibot_lite import NeoPixel            # Assuming NeoPixel is saved as neopixel.py
from romer_minibot_lite import Button         # Assuming Button is saved as button.py

# Initialize the Accelerometer
sda_pin = 12  # Replace with your SDA pin
scl_pin = 13  # Replace with your SCL pin
delta_time = 100  # Interval in milliseconds between readings

accelerometer = Accelerometer(sda=sda_pin, scl=scl_pin, delta_time=delta_time)

# Initialize the NeoPixel strip
neopixel_pin = 0  # Replace with your NeoPixel data pin
num_pixels = 20    # Number of LEDs in your NeoPixel strip
neopixel_strip = NeoPixel(pin_number=neopixel_pin, num_pixels=num_pixels)

# Initialize the Button
button_pin = 3  # Replace with your button pin
button = Button(pin_number=button_pin, mode='pull_up', invert=False, debounce_ms=60)

# Function to map accelerometer values to RGB
def map_to_rgb(x, y, z):
    # Assuming the range of x, y, z is -256 to 256
    r = int((x + 256) * (255 / 512))  # Map -256 to 256 into 0-255 for red
    g = int((y + 256) * (255 / 512))  # Map -256 to 256 into 0-255 for green
    b = int((z + 256) * (255 / 512))  # Map -256 to 256 into 0-255 for blue
    return r, g, b

# Main loop to control NeoPixels based on accelerometer data
while True:
    if not button.state:  # Button is pressed when state is True (invert if needed)
        # Set all NeoPixels to red when the button is pressed
        pixel_colors = [(i, (255, 0, 0)) for i in range(num_pixels)]  # Red color

    else:
        # Read accelerometer values
        x, y, z = accelerometer.read_accel_data()
        
        # Map accelerometer values to RGB
        r, g, b = map_to_rgb(x, y, z)

        # Create a list of RGB values to fill all NeoPixels
        pixel_colors = [(i, (r, g, b)) for i in range(num_pixels)]  # Fill all pixels with the same color

    # Update NeoPixels with the calculated RGB values
    neopixel_strip.fillwith(pixel_colors, brightness=0.5)

    # Print the RGB values and accelerometer data for debugging
    print(f"Accelerometer data -> X: {x}, Y: {y}, Z: {z}")
    print(f"RGB values -> R: {r}, G: {g}, B: {b}")

    # Wait for the next reading
    time.sleep(delta_time / 1000)

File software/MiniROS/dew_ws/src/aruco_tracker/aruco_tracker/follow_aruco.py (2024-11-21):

import rclpy
from rclpy.node import Node
from geometry_msgs.msg import Twist, PolygonStamped
import numpy as np
from rclpy.timer import Timer
from std_msgs.msg import Bool

class FollowAruco(Node):
    def __init__(self):
        super().__init__('follow_aruco')
        self.subscription = self.create_subscription(
            PolygonStamped,
            'aruco_marker',
            self.listener_callback,
            10)
        self.publisher_ = self.create_publisher(Twist, '/cmd_vel_aruco', 10)
        self.sobe_publisher = self.create_publisher(Bool, 'sobe', 10)
        self.subscription  # prevent unused variable warning
        self.publisher_  # prevent unused variable warning
        self.sobe_publisher  # prevent unused variable warning

        self.last_marker_time = self.get_clock().now()
        self.no_marker_timeout = 2.0  # seconds without marker before rotating
        self.timer = self.create_timer(0.1, self.check_marker_timeout)

    def listener_callback(self, msg):
        if msg.polygon.points:
            self.last_marker_time = self.get_clock().now()
            self.get_logger().info(f'Received marker corners {msg.polygon.points}')

            # Calculate the center of the marker
            corners = [(point.x, point.y) for point in msg.polygon.points]
            corners = np.array(corners)
            cX, cY = np.mean(corners, axis=0)

            # Calculate the size of the marker (using the distance between two opposite corners)
            size = np.linalg.norm(corners[0] - corners[2])
            
            self.get_logger().info(f'size{size}')

            # Image dimensions (assuming some known width)
            w = 640  # Replace with your camera's width
            self.get_logger().info(f'center: {cX}')

            if cX > w / 2:
                angular_velocity = -0.00005 * (cX - w / 2)
            else:
                angular_velocity = -0.00003 * (cX - w / 2)
            # Calculate angular velocity based on marker center position
            # angular_velocity = -0.000009 * (cX - w / 2)
            # angular_velocity = 0.0 * (cX - w / 2)
            # Calculate linear velocity based on marker size
            reference_size = 350  # Size of the marker at the desired distance
            max_linear_velocity = 0.4  # Maximum linear velocity
            min_linear_velocity = 0.05  # Minimum linear velocity

            if size < reference_size:
                print(f'size: {size}')
                linear_velocity = 0.0004 * (reference_size - size)
                if linear_velocity < 0.075:
                    linear_velocity = 0.075
                self.publish_sobe(False)      

            else:
                linear_velocity = 0.0
                angular_velocity = 0.0
                self.publish_sobe(True)
            if linear_velocity < min_linear_velocity:
                self.get_logger().info(f'I am here')
                linear_velocity = 0.0
                angular_velocity = 0.0 
                self.publish_sobe(True)      
            # Publish the calculated velocities
            self.publish_velocity(linear_velocity, angular_velocity)
        else:
            self.get_logger().info('No marker detected')

    def publish_velocity(self, linear_velocity, angular_velocity):
        twist = Twist()
        twist.linear.x = linear_velocity
        twist.angular.z = angular_velocity

        # Debugging information
        self.get_logger().info(f'Linear velocity: {twist.linear.x}')
        self.get_logger().info(f'Angular velocity: {twist.angular.z}')

        self.publisher_.publish(twist)

    def publish_sobe(self, state):
        sobe_msg = Bool()
        sobe_msg.data = state
        self.sobe_publisher.publish(sobe_msg)
        self.get_logger().info(f'Published "sobe" message with state: {state}')      

    def check_marker_timeout(self):
        current_time = self.get_clock().now()
        time_since_last_marker = (current_time - self.last_marker_time).nanoseconds/1e9
        if time_since_last_marker > self.no_marker_timeout:
            self.get_logger().info('No marker detected for a while, rotating to search')
            self.publish_velocity(0.0, 0.099)  # Rotate in place
            self.publish_sobe(False)      


def main(args=None):
    rclpy.init(args=args)
    follow_aruco = FollowAruco()
    rclpy.spin(follow_aruco)
    follow_aruco.destroy_node()
    rclpy.shutdown()

if __name__ == '__main__':
    main()

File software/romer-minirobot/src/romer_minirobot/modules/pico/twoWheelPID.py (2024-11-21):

from machine import Pin, PWM
from utime import ticks_ms
import rp2
from ...urtps.node import Node
from .encoder import Encoder
        
class TwoWheelPID(Node):
    """
    A class representing a two-wheel PID controller for motor control.

    Args:
        dt (float): The time interval between control updates in seconds. Default is 0.3 seconds.

    Attributes:
        motor1_pin2 (PWM): The PWM object representing the control pin for motor 1.
        motor1_pin1 (PWM): The PWM object representing the control pin for motor 1.
        motor2_pin2 (PWM): The PWM object representing the control pin for motor 2.
        motor2_pin1 (PWM): The PWM object representing the control pin for motor 2.
        motor1_hall_1 (Pin): The Pin object representing the hall sensor input for motor 1.
        motor1_hall_2 (Pin): The Pin object representing the hall sensor input for motor 1.
        motor2_hall_1 (Pin): The Pin object representing the hall sensor input for motor 2.
        motor2_hall_2 (Pin): The Pin object representing the hall sensor input for motor 2.
        pi1 (PI): The PI controller object for motor 1.
        pi2 (PI): The PI controller object for motor 2.
        last_time (int): The timestamp of the last control update.
        dt (float): The time interval between control updates in seconds.

    """

    def __init__(self, name = 'twoWheel', dt=0.3):
        super().__init__(name, 'subscribing')
        # Define motor control pins
        self.motor1_pin2 = PWM(Pin(6, Pin.OUT))
        self.motor1_pin1 = PWM(Pin(7, Pin.OUT))
        self.motor2_pin2 = PWM(Pin(20, Pin.OUT))
        self.motor2_pin1 = PWM(Pin(19, Pin.OUT))
        # Set the frequency of the PWM signal
        self.motor1_pin1.freq(100000)
        self.motor1_pin2.freq(100000)
        self.motor2_pin1.freq(100000)
        self.motor2_pin2.freq(100000)

        self.motor1_hall_1 = Pin(4, Pin.IN, Pin.PULL_UP)
        self.motor1_hall_2 = Pin(5, Pin.IN, Pin.PULL_UP)
        self.motor2_hall_1 = Pin(21, Pin.IN, Pin.PULL_UP)
        self.motor2_hall_2 = Pin(22, Pin.IN, Pin.PULL_UP)

        self.pid1 = PID(A=4, B=5, prop=85000, integ=500, deriv=0)
        self.pid2 = PID(A=22, B=21, prop=80000, integ=600, deriv=200)

        self.last_time = 0
        self.dt = dt
        
        self.RPM = 200
        self.RPS = self.RPM / 60
        
    def motor1_write(self, duty_cycle, direction):
        """
        Set the duty cycle and direction of motor 1.

        Args:
            duty_cycle (int): The duty cycle value between 0 and 65535.
            direction (bool): The direction of rotation. True for forward, False for backward.

        """
        if direction:
            self.motor1_pin1.duty_u16(duty_cycle)
            self.motor1_pin2.duty_u16(0)
        else:
            self.motor1_pin1.duty_u16(0)
            self.motor1_pin2.duty_u16(duty_cycle)

    def motor2_write(self, duty_cycle, direction):
        """
        Set the duty cycle and direction of motor 2.

        Args:
            duty_cycle (int): The duty cycle value between 0 and 65535.
            direction (bool): The direction of rotation. True for forward, False for backward.

        """
        if direction:
            self.motor2_pin1.duty_u16(duty_cycle)
            self.motor2_pin2.duty_u16(0)
        else:
            self.motor2_pin1.duty_u16(0)
            self.motor2_pin2.duty_u16(duty_cycle)

    async def tick(self):
        """
        Perform a control update.

        This method is called periodically to update the motor control based on the received message.

        """
        cur_time = ticks_ms()
        if self.get_message():

            x_linear, z_angular = self.get_message().split(",")  # what will be the unit for this???
            
            x_linear = float(x_linear) * self.RPS
            z_angular = float(z_angular) * self.RPS

            self.pid1.set_ref_speed(x_linear + z_angular)
            self.pid2.set_ref_speed(x_linear - z_angular)

            #print(self.pid1.ref_speed, self.pid2.ref_speed)
        # print(f'motor1:{self.pid1.speed},motor2:{self.pid2.speed}')
        
        if cur_time - self.last_time > self.dt:
            self.pid1.update()
            self.pid2.update()
            motor1_speed = self.pid1.pid()
            motor2_speed = self.pid2.pid()
            #print(f'motor1ref:{self.pid1.ref_speed},motor1speed:{self.pid1.speed}')
            #print(f'motor2^ref:{self.pid2.ref_speed},motor2speed:{self.pid2.speed}')
            self.motor1_write(int(abs(motor1_speed)), motor1_speed > 0)
            self.motor2_write(int(abs(motor2_speed)), motor2_speed > 0)
        self.set_message(None)
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

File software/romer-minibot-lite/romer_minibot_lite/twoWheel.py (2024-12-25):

from machine import Pin, PWM

        
class TwoWheel():
    """
    A class representing a two-wheel motor controller.

    Args:
        motor1_pins (tuple): A tuple containing the GPIO pins for motor 1 in the format (pin1, pin2).
        motor2_pins (tuple): A tuple containing the GPIO pins for motor 2 in the format (pin1, pin2).
        freq (int): The frequency of the PWM signal in Hz.
        scale (float): The scale factor for the motor speed. The range of valid values is (-scale, scale).

    Example:
        To create a TwoWheel object with motor 1 connected to GPIO pins 6 and 7, motor 2 connected to GPIO pins 19 and 20,
        a frequency of 1000 Hz, and a scale factor of 1.0, you can do the following:

        >>> two_wheel = TwoWheel(motor1_pins=(6, 7), motor2_pins=(19, 20), freq=1000, scale=1.0)
    """

    def __init__(self, motor1_pins=(6, 7), motor2_pins=(20, 19), freq=1000, scale=1.0):
        # Define motor control pins
        self.motor1_pin2 = PWM(Pin(motor1_pins[0], Pin.OUT))
        self.motor1_pin1 = PWM(Pin(motor1_pins[1], Pin.OUT))
        self.motor2_pin2 = PWM(Pin(motor2_pins[0], Pin.OUT))
        self.motor2_pin1 = PWM(Pin(motor2_pins[1], Pin.OUT))
        # Set the frequency of the PWM signal
        self.motor1_pin1.freq(freq)
        self.motor1_pin2.freq(freq)
        self.motor2_pin1.freq(freq)
        self.motor2_pin2.freq(freq)
        self.scale = scale

    def motor1_write(self, duty_cycle, direction):
        """
        Set the duty cycle and direction of motor 1.

        Args:
            duty_cycle (int): The duty cycle of the PWM signal for motor 1. Valid range is 0 to 65535.
            direction (bool): The direction of rotation for motor 1. True for forward, False for backward.

        Example:
            To set the duty cycle of motor 1 to 5000 and rotate it forward, you can do the following:

            >>> two_wheel.motor1_write(5000, True)
        """
        if direction:
            self.motor1_pin1.duty_u16(duty_cycle)
            self.motor1_pin2.duty_u16(0)
        else:
            self.motor1_pin1.duty_u16(0)
            self.motor1_pin2.duty_u16(duty_cycle)

    def motor2_write(self, duty_cycle, direction):
        """
        Set the duty cycle and direction of motor 2.

        Args:
            duty_cycle (int): The duty cycle of the PWM signal for motor 2. Valid range is 0 to 65535.
            direction (bool): The direction of rotation for motor 2. True for forward, False for backward.

        Example:
            To set the duty cycle of motor 2 to 8000 and rotate it backward, you can do the following:

            >>> two_wheel.motor2_write(8000, False)
        """
        if direction:
            self.motor2_pin1.duty_u16(duty_cycle)
            self.motor2_pin2.duty_u16(0)
        else:
            self.motor2_pin1.duty_u16(0)
            self.motor2_pin2.duty_u16(duty_cycle)

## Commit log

2024-11-21 cad moved to hardware
    [Roller.STL, battery_holder.prt, camholder.prt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]
2024-11-21 Ros part is uploaded'
    [ball_tracker_params_robot.yaml, camera.xacro, gazebo_control.xacro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]
2024-12-25 Add files via upload
    me220 version of pico library is uploaded
